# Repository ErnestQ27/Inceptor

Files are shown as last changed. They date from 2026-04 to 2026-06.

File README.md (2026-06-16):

# Inceptor
An RC, modular, fixed-wing, dual-motor, 3D-printable aircraft capable of several configurations. I want to be able to have a flight platform capable of hosting a diverse set of missions on a singular base unit with a selection of wings, tails, noses, and other components.

The purpose of Inceptor is to allow users to purchase or build a modular aircraft and customize components tailored to their needs. Inceptor: Base V1 provides users with the ability to have a core, functioning unit intended to demonstrate modular ability in swapping batteries, ESCs, Flight Computer programs, and motors. Later version upgrades will allow users to instead print out different wings, a different tail, a different nose, different payload bay size, etc.

*Note that in future upgrades, you will be able to have a choice between which of each section's variation you would like to have (e.g, a longer variation of LW and RW).*

# Assembly for Inceptor: Base V1
**Setup**

1. Print all necessary 3D files
2. Purchase and/or obtain BOM and necessary tools (optionally heated insert tool)
3. Cut music wire into 2 sections of 180mm and 2 sections of 100mm
4. Cut carbon fiber tube into 2 sections of 450mm and 2 sections of 550mm

**VTail**

1. Insert servos into appropiate positions and run wire into hole of VT-Block
2. Ensure servos are in neutral position and connect servo horns
3. Connect VT-L-Ruddervator and VT-R-Ruddervator to appropriate servo
4. Insert 100mm music wire sections into Ruddervators
5. Apply glue to long, flat side of VT-L and VT-R (part that touches VT-Block)
6. Slide VT-L and VT-R onto the music wire and attach to VT-Block, referencing the CAD
7. Slide both 550mm carbon fiber longerons onto VT-Block
8. Connect servo wire extensions on both sides

Result should look like this (wires not included):


**Wings**
1. Slide the far ends of each wing onto an indivudal 450mm carbon tube
2. Slide on the wing sections meant to go in front of each aileron, attach with glue
3. Insert a 180mm music wire section onto the far end wing pieces
4. Insert servos into appropriae positions and run wires into rectangular section of each wing
5. Ensure servos are in neutral position and connect servo horns
6. Connect ailerons to each servo horn
7. Attach servos' wing sections to currently assembled wing with glue, ensure aileron has music wire running through it
8. Apply heated inserts to motor blocks, use grub screws to attach motors
9. Attach motor blocks with motor onto respective carbon spars, attach with glue and ensure wires run through to rectangular section
10. Connect servo and motor wire extensions on both sides
11. Result for left wing (so far) should look like this (wires not included):
    
    
13. Slide remaining sections and attach with glue, referencing the CAD and keeping wires available

Result for left wing should look like this (wires not included):


**Fuselage**
1. Apply heated inserts to all respective holes on both wing attachments, starting from the inside
2. Slide on Payload Section Back to VT-Block, Payload Section Front, and Section 3, attach all to each other with glue
3. Holding Core Section Front, Wing Rod Stops, and Battery Tray in their positions relative to one another, referencing the CAD, slide onto the rest of the fuselage
4. Place battery in Battery Tray and secure with velcro straps
5. Add RX to Arduino Mount, and, optionally, add an Arduino
6. Screw Section 3 and Core Section Front onto Wing Attachment, ensure assembly looks like this so far (wires not included):
   

7. Fit Nose Cone Adapter onto longerons and ensure snap fit cantilevers are in Wing Attachments, referencing CAD
8. Fit Nose Cone onto longerons, attach to Nose Cone Adapter with glue
9. Connect both motor wire extensions to ESCs, connect ESCs to battery's XT60 via a Y-harness
10. Connect all servo wires to correct channel on RX, reference the Wiring Diagram
11. Fully slide wings onto each Wing Attachment and into Wing Rod Stops
12. Snap on Core Section Bottom, referencing the CAD, and attach with glue
13. Snap on Core Section Top

Result should look like this (wires and RX not included, Core Section Top made transparent):


# Wiring
**Diagram:** 

Connect the servo extensions to all 4 servos. Connect the Female to Male 3-Phase Wire extensions to both motors' wires and to ESCs. Connect XT60 Y-Harness to ESCs and Battery. Disactivate BEC from Left Wing's ESC via disconnecting live wire, connect Right Wing ESC's signal wires to Left Wing ESC's via a Y-harness and connect to Channel 3. Connect VTail's left servo extension to Channel 4 and the right one to Channel 2. Connect Right Wing's servo wires to Left Wing's via connecting their extensions via Y-Harness and connecting to Channel 1. Set TX up for VTail configuration, and ensure all control surfaces and throttle work as intended, if not, simply reverse wire connection.

*Note: A detailed video tutorial will be provided once and while I assemble my own Inceptor prototype, along with values for Center of Gravity, weight, and other performance characteristics*

# OnShape CAD:
**Link:** https://cad.onshape.com/documents/1e6ea4fb9d6a4182b08372fd/w/82ca669ecb5636d0f431f821/e/5a5b780a35879ddb0144018a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

**Images** 

Top View: 

Right View: 

Front View: 

Isometric View: 

# BOM (Inceptor: Base V1)
**Link:**
[BOM.csv](https://github.com/user-attachments/files/27289383/BOM.csv)

**Components, Total Price, and Quantity to Obtain**

CW A2212 Motor---------------$10.99-1

CCW A2212 Motor--------------$10.99-1

4S Battery-----------------------$26.99-1

MG90S Servo--------------------$9.98-4

CC/CCW 9045 Propellers--------$2.99--1       

40A ESC w/ BEC-----------------$25.98-2

8x6mm 1m CF Tube-------------$16.72-2

M3x5 Heated Insert--------------$1.60-16

M3x10 Phillips Pan Head Screw-$0.56-8

M3x10 Grub Screw---------------$0.72-8

Epoxy Resin Glue and Hardener-$6.78-1

FlySky FSi6/iA6 TX/RX------------$49.99-1

1.5mm Music Wire----------------$4.59-1

Servo Wire Y-Harness------------$3.58-2

500mm Servo Wire Extensions---$0.99-4

Battery Velcro Strap---------------$0.99-1

**Total Upper-End (exclusive of shipping + taxes): *$181.22***

# Zine Page
INCEPTOR (5 83 x 8 27 in)

*Real pictures and videos coming soon, for your convenience!!!*

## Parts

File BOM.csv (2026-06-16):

Component | Link | Price | Quantity
CW A2212 Motor | https://sunnyskyusa.com/products/sunnysky-a2212-motors-multirotor-version?variant=15989280931934 | $10.99 | 1
CCW A2212 Motor | https://sunnyskyusa.com/products/sunnysky-a2212-motors-multirotor-version?variant=15989301772382 | $10.99 | 1
4S Battery | https://www.roaringtopusa.com/25C-3500MAH-4S-LIPO | $26.99 | 1
MG90S Servo | https://www.walmart.com/ip/4Pcs-Updated-MG90S-Servo-Motor-LINKPAL-MG90S-Metal-Geared-RC-Micro-Servo-Motor-9G-Compatible-for-RC-Model-Helicopter-Airplane-Remot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 | $9.98 | 4
CW/CCW 9045 Propeller | https://sunnyskyusa.com/products/sunnysky-multirotor-9450-propellers-cw-ccw-rotation-pair-fit-a2212-x2212-multirotor-motors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 | $2.99 | 1
40A ESC w/ BEC | https://www.amazon.com/Brushless-Controller-Airplanes-Multi-axis-Helicopter/dp/B0CN317H74 | $25.98 | 2
8x6mm 1m CF Tube | https://www.readymaderc.com/products/details/carbon-fiber-tube-8mm-x-6mm-1m-long?gad_source=1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 | $16.72 | 2
M3x5 Heated Insert | https://kb-3d.com/store/inserts-fasteners-adhesives/278-brass-heat-set-threaded-insert-for-plastic-m3x5x4mm.html | $1.60 | 16
M3x10 Phillips Pan Head Screw | https://boltdepot.com/Product-Details?product=17868 | 0.56 | 8
M3x10 Grub Screw | https://boltdepot.com/Product-Details?product=8709 | 0.72 | 8
Epoxy Glue | https://www.walmart.com/ip/Gorilla-Glue-Epoxy-0-85-Ounce-Syringe-Two-Part-Resin-and-Hardener/626168582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 | 13.56 | 2
FlySky FS i6/iA6 TX/RX | https://www.amazon.com/Flysky-Transmitter-Controller-Helicopter-Quadcopter/dp/B07CWBQ2HM?th=1 | 49.99 | 1
1.5mm Music Wire | https://windcatcherrc.com/product/1-5mm-od-x-1meter-long-5pc-music-wire-ks-precision-metals-copy/?gad_source=1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 | 4.59 | 1
Servo Y-Harness | https://www.buddyrc.com/products/futaba-compatible-servo-y-splitter-extension-cable-150mm | $3.58 | 2
500mm Servo Wire Extensions | https://www.aliexpress.us/item/3256810149439102.html?gatewayAdapt=glo2usa4itemAdapt | 0.99 | 4
Battery Velcro Strap | https://www.aliexpress.us/item/2251832287004624.html?curPageLogUid=qAeQSSRC1EA2 | 0.99 | 1
 |  | $209.21

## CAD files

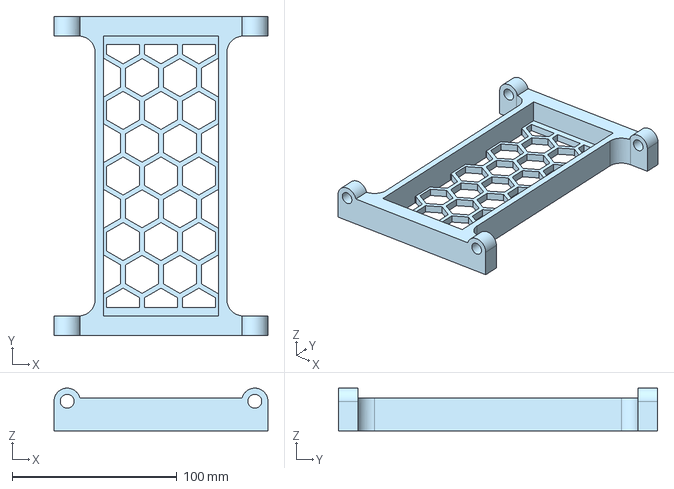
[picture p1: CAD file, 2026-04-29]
3D Printed Parts/Core Unit Slider/Core Unit Slider - Battery Tray.step
130.0 x 194.0 x 26.0 mm

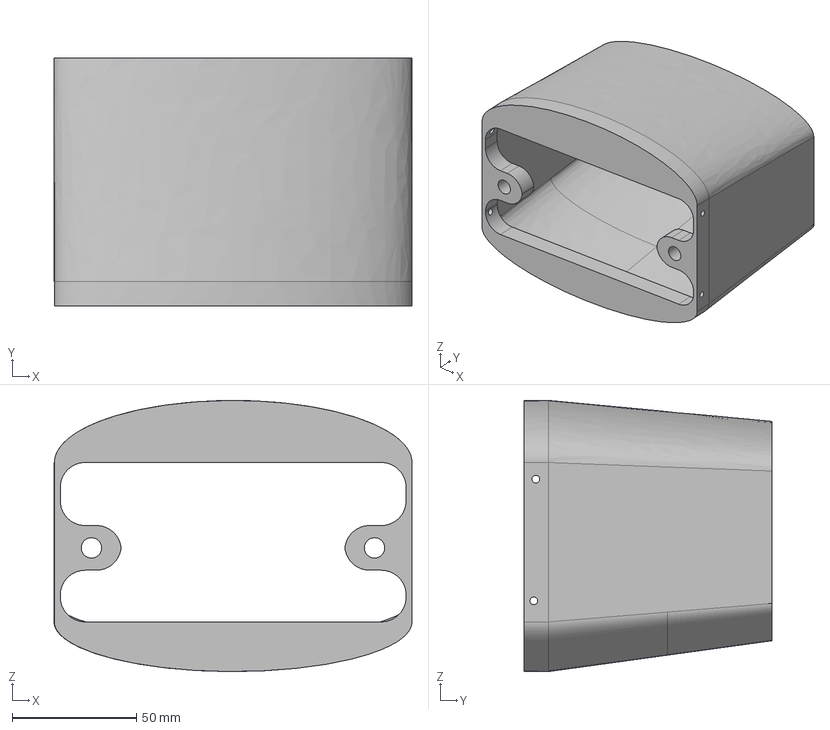
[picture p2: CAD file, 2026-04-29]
3D Printed Parts/Fuselage/Fuselage - Section 3.step
144.2 x 100.0 x 109.2 mm

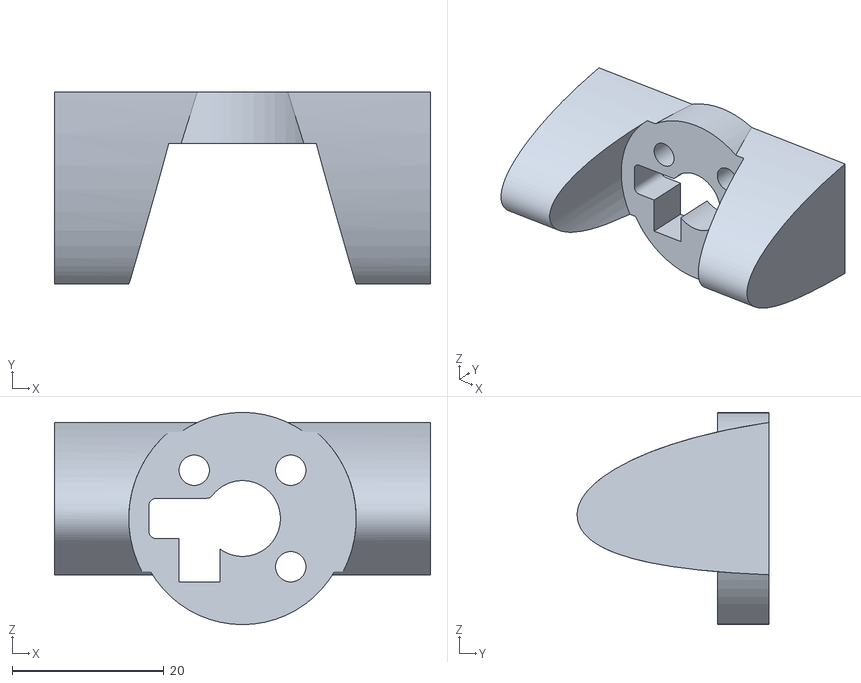
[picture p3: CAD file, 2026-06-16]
3D Printed Parts/Left Wing/Left Wing - LWM.stl
49.6 x 25.3 x 28.0

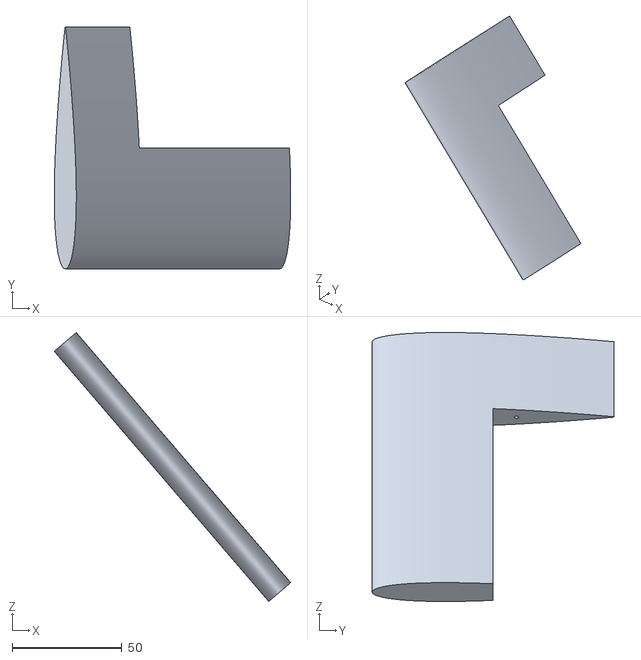
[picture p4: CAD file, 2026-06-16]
3D Printed Parts/VTail/VTail - VT-L.stl
107.7 x 110.0 x 122.5

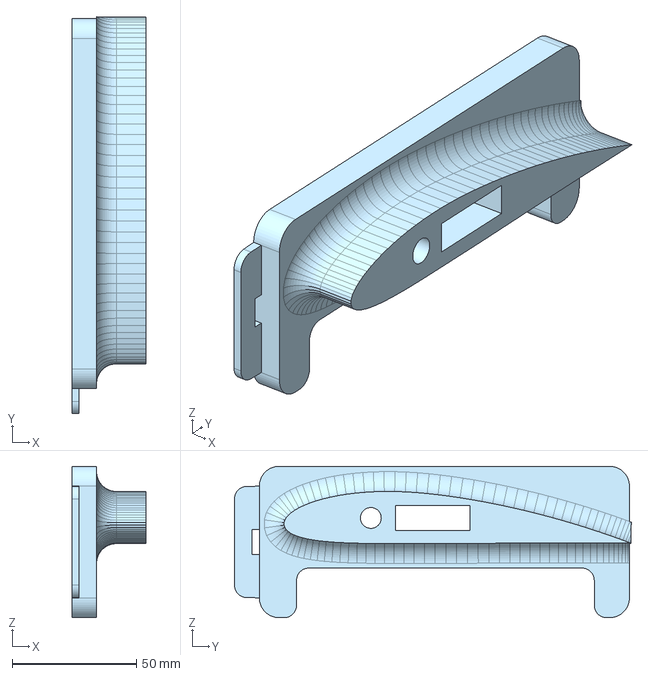
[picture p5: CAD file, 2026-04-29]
3D Printed Parts/Fuselage/Fuselage - Wing Attachment L.step
30.0 x 160.0 x 61.0 mm

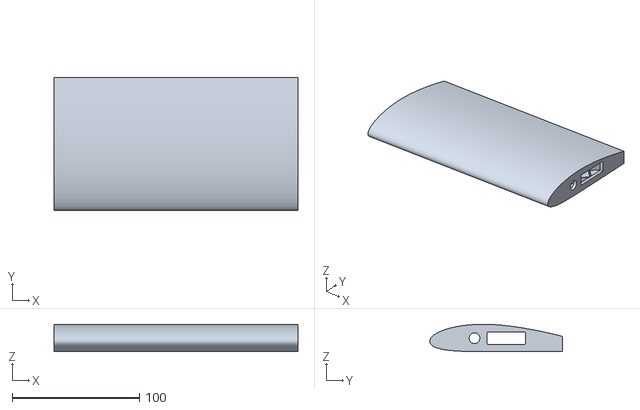
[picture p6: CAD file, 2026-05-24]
3D Printed Parts/Left Wing/Left Wing - LW-J.stl
192.0 x 104.3 x 21.5

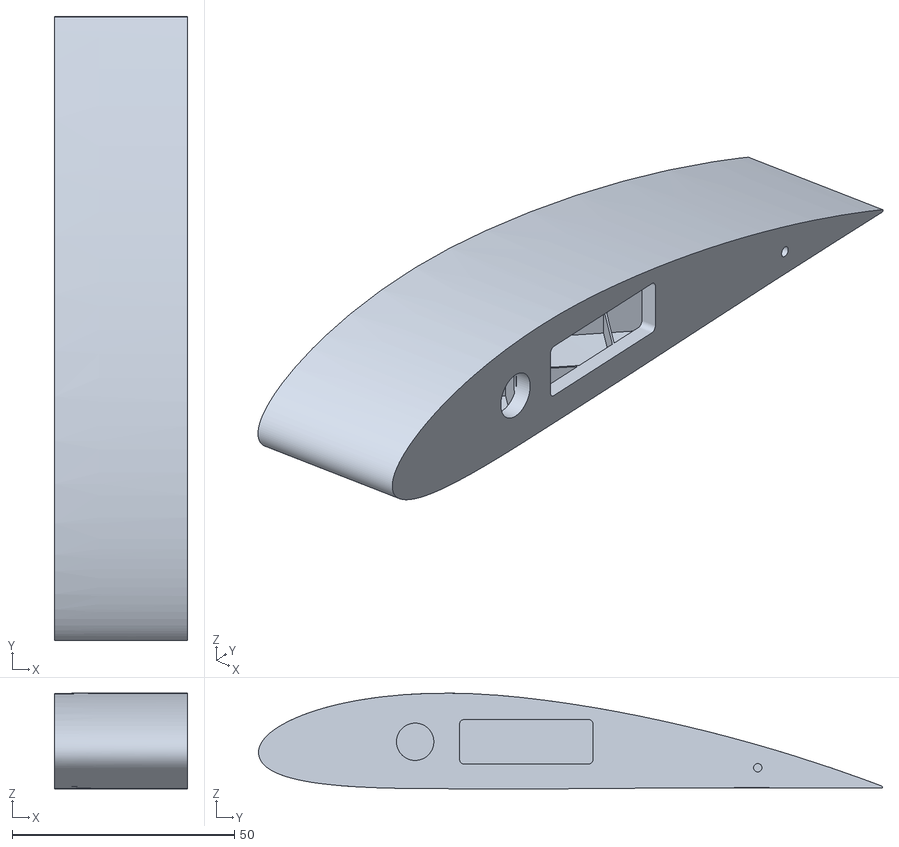
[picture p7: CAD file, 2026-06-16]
3D Printed Parts/Right Wing/Right Wing - RW-G.stl
30.0 x 140.3 x 21.5

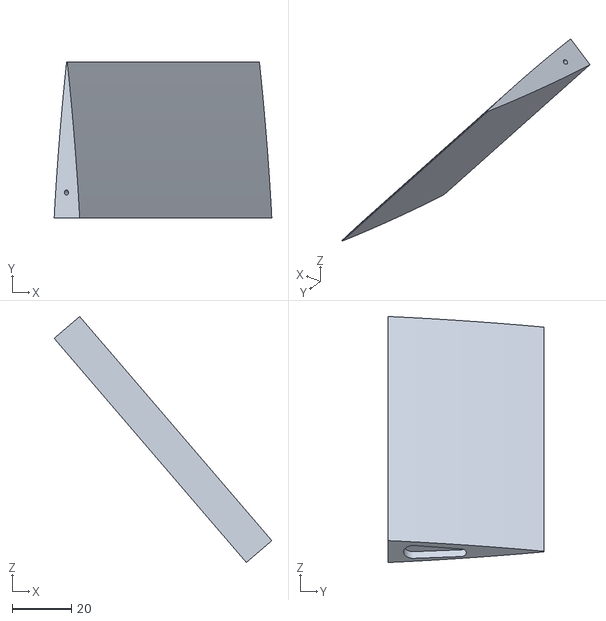
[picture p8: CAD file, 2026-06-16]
3D Printed Parts/VTail/VTail - VT-R-Ruddervator.stl
73.7 x 53.0 x 83.3

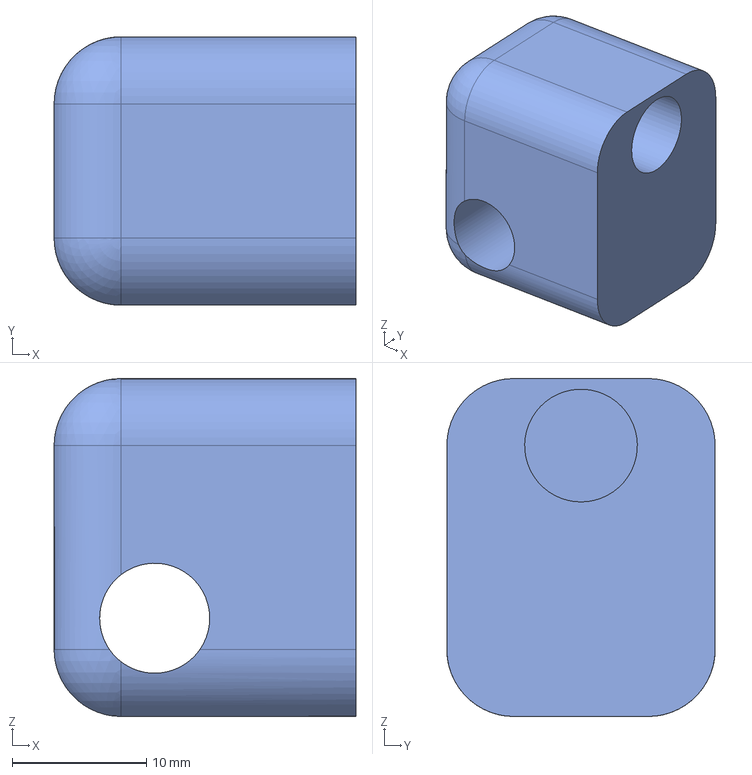
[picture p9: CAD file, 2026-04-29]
3D Printed Parts/Fuselage/Fuselage - Wing Rod Stop L.step
22.5 x 20.0 x 25.2 mm

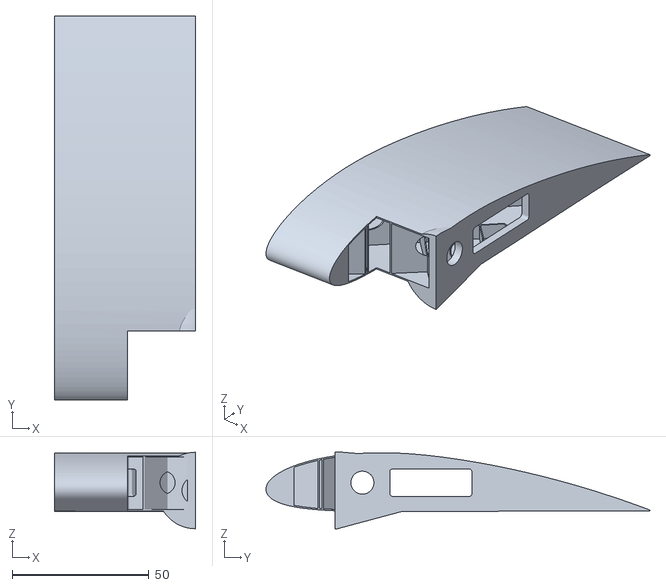
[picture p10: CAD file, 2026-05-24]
3D Printed Parts/Left Wing/Left Wing - LW-I-R.stl
51.7 x 140.3 x 28.0

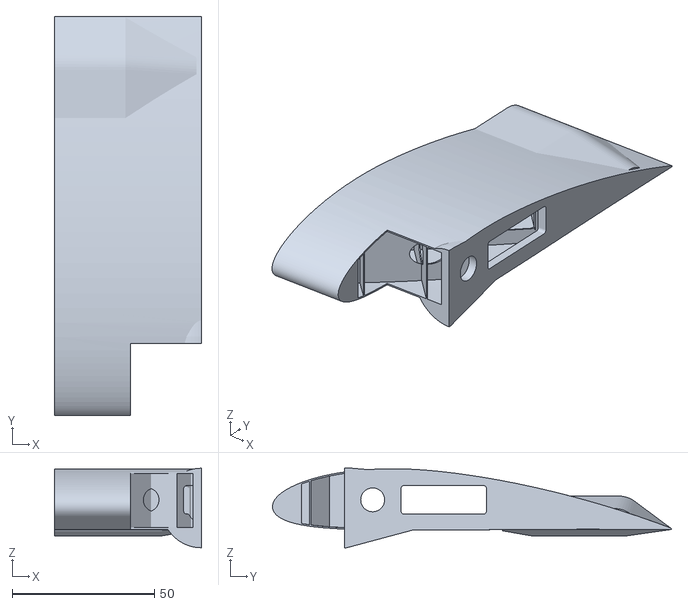
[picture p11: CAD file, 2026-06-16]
3D Printed Parts/Right Wing/Right Wing - RW-E-R.stl
51.7 x 140.3 x 28.0

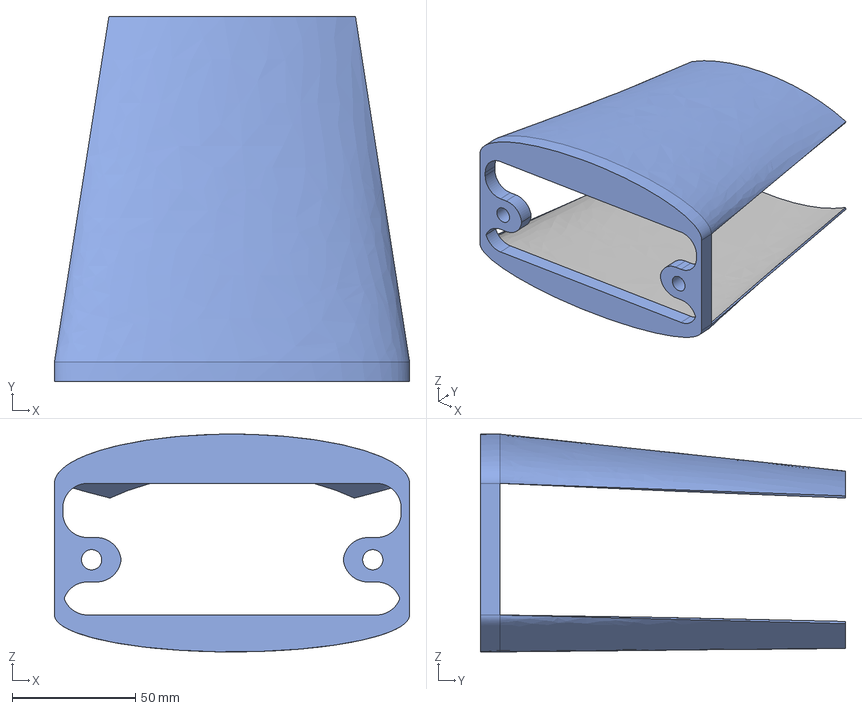
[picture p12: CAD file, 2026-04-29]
3D Printed Parts/Fuselage/Fuselage - Payload Section Front.step
144.0 x 148.0 x 88.3 mm

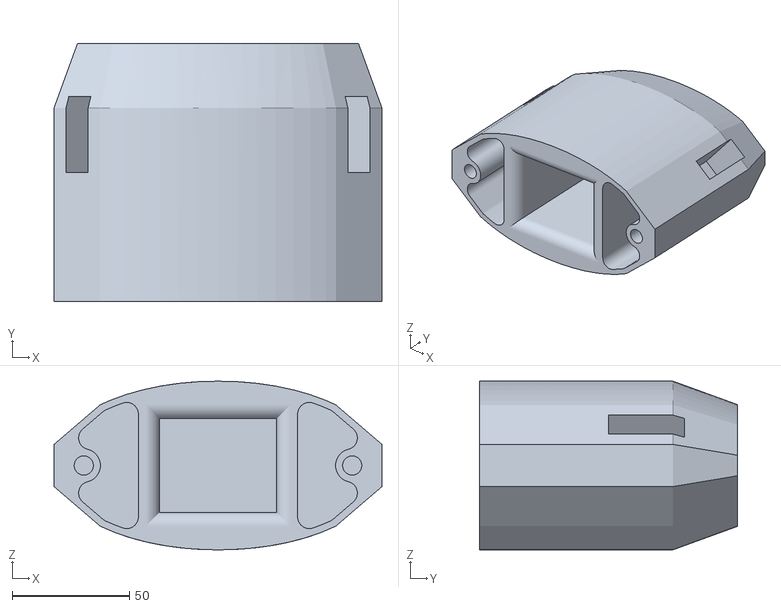
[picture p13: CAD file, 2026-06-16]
3D Printed Parts/VTail/VTail - VT-Block.stl
140.0 x 110.0 x 72.0

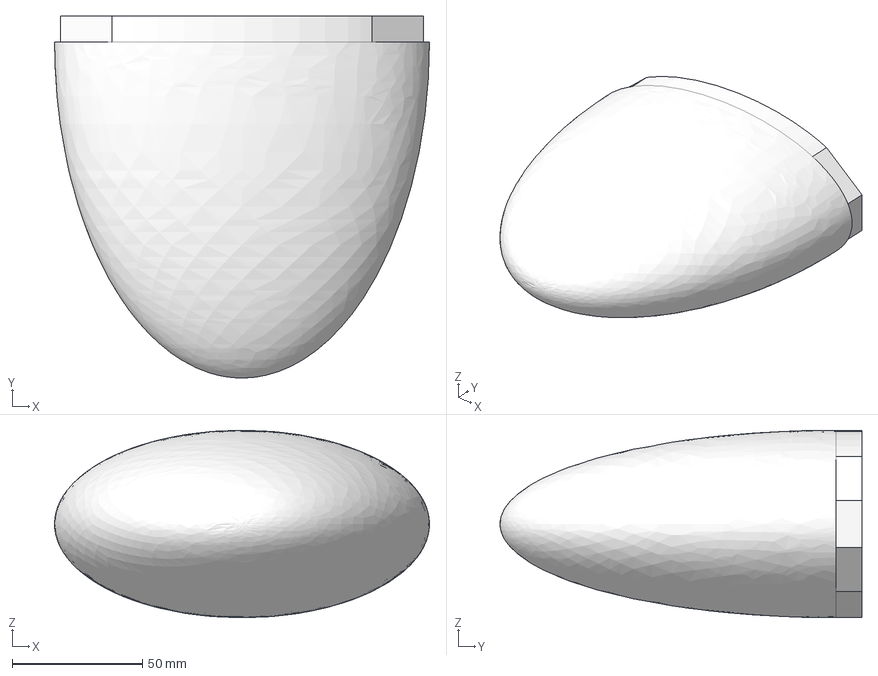
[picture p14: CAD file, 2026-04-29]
3D Printed Parts/Fuselage/Fuselage - Nose Cone.step
144.0 x 139.0 x 72.0 mm

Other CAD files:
3D Printed Parts/Right Wing/Right Wing - RWM.stl
3D Printed Parts/VTail/VTail - VT-R.stl
3D Printed Parts/Left Wing/Left Wing - LW-K.stl
3D Printed Parts/Right Wing/Right Wing - RW-E-L.stl
3D Printed Parts/Fuselage/Fuselage - Core Section Bottom.step
3D Printed Parts/Fuselage/Fuselage - Core Section Front.step
3D Printed Parts/Fuselage/Fuselage - Core Section Top.step
3D Printed Parts/Fuselage/Fuselage - Nose Cone Adapter.step
3D Printed Parts/Fuselage/Fuselage - Payload Section Back.step
3D Printed Parts/Fuselage/Fuselage - Wing Attachment R.step
3D Printed Parts/Fuselage/Fuselage - Wing Rod Stop R.step
3D Printed Parts/Left Wing/Left Wing - LW-H.stl
3D Printed Parts/Left Wing/Left Wing - LW-I-L.stl
3D Printed Parts/Left Wing/Left Wing - LWA.stl
3D Printed Parts/Right Wing/Right Wing - RW-D.stl
3D Printed Parts/Right Wing/Right Wing - RW-F.stl
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

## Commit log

2026-04-29 Add CAD link to README for Inceptor project
    Added OnShape CAD link for the Inceptor aircraft.
2026-04-29 Add files via upload
    First release of Inceptor: Base's CAD model
2026-04-29 Add files via upload
    Unzipped the CAD files for ease of use.
    [Arduino Mount - Bottom.step, Arduino Mount - Top.step, Core Unit Slider - Battery Tray.step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]
2026-04-29 Fix formatting of OnShape CAD Link in README
2026-04-29 Enhance README with CAD link and images
    Updated the OnShape CAD link format and added images of the aircraft from different views.
2026-04-29 Revise README with project details and BOM
    Updated project description for clarity and added a Bill of Materials (BOM) section with component details and pricing.
2026-04-30 Revise BOM link and total price in README
    Updated BOM link and added new components with pricing.
2026-04-30 Enhance README with assembly instructions for Inceptor
    Expanded the README to include detailed assembly instructions for Inceptor: Base V1, including setup steps and VTail assembly.
2026-05-01 Revise assembly instructions and BOM link
    Updated assembly instructions for wings and fuselage, added wiring details, and corrected BOM link.
2026-05-01 Update BOM link and fix component formatting
    Updated the BOM link and corrected formatting for components.
2026-05-15 Revise wiring diagram and connection instructions
    Updated wiring diagram and instructions for clarity.
2026-05-24 Clarify motor block attachment instructions
2026-05-24 Replace right wing image in README
    Updated image reference for right wing result in README.
2026-05-24 Revise left wing assembly instructions and images
    Updated images for left wing assembly and adjusted step numbering.
2026-06-16 Update BOM.csv with new components and prices
    [BOM.csv]
2026-06-16 Reorganize assembly steps in README
    Reordered steps in the assembly instructions for clarity and consistency.
2026-06-16 Update images in assembly instructions
2026-06-16 Update component list and total cost in README
    Removed Arduino from the list of components and updated the total cost accordingly.
